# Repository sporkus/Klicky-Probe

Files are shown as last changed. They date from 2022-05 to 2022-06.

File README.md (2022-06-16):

# Klicky Probe
Microswitch probe with magnetic attachment, primarily aimed at CoreXY 3d printers.

Initially it was focused on the [Voron printers](https://vorondesign.com/) (V2.4, V1.8, Trident, V0) and derivatives, now it's been restructured to better allow other printers to be documented here.

The objectives for this project are:
- drop in replacement for Omron TL-Q5MC2 or PL-08N2 (you don't need to replace the toolhead), replacement of BLtouch probes
- soldering not required
- minimal adjustments required
- be able to detect all the print surfaces
- be as close to the hotend tip as possible
- highly repeatable and accurate probes
- less temperature variations
- no melting of its parts
- cheap to build
- reuse spare parts if possible

Most of the Klicky probe users are using klipper, there are some macros in here that ease the probing process, by automating the attach, dock and use of the probe.

Some work has been developed to have the same functionality on RRF.

It can also be used with the [automatic Z calibration](https://github.com/protoloft/klipper_z_calibration) klipper plugin to effectively calculate the Z offset from the probe and from the Z endstop if your printers supports a Z endstop triggered by the nozzle (like most Voron's do)

The inspiration for the Klicky Probe comes from the [Quickdraw](https://github.com/Annex-Engineering/Quickdraw_Probe) and the [Euclid probe](https://github.com/nionio6915/Euclid_Probe), it uses some concepts from each of the projects.

Updated instructions provided by StefanRaatz.
oc_geek and TurBoxxs were also a great help in refining and testing the CAD files.
Garrettwp provided the initial revised macro files.
User richardjm revised the macro variables and added some functions.
Mental created the initial macro and one of the first magnetically attached microswitch probes.

Without them, and some others this effort would not be in the current state, many thanks to them all.

It is working very well, if you decide to use it, give me feedback, either here, or on discord, my discord user is JosAr#0517.

If you want to donate something regarding this project, use this [link](https://paypal.me/Josar154) or [__Buy me some ABS!__](https://www.buymeacoffee.com/JosAr), thanks

# Upgrading from an earlier version

If you are upgrading from an earlier version, check the [klipper macros](./Klipper_macros) folder, it contains update instructions.

# Probe options

Right now, there are two probe attachment options, each with two probe types.

## Regular Klicky

First klicky probe, based on the [Quickdraw probe](https://github.com/Annex-Engineering/Quickdraw_Probe), with an added third magnet for added stability and fixed dock gantry setups.

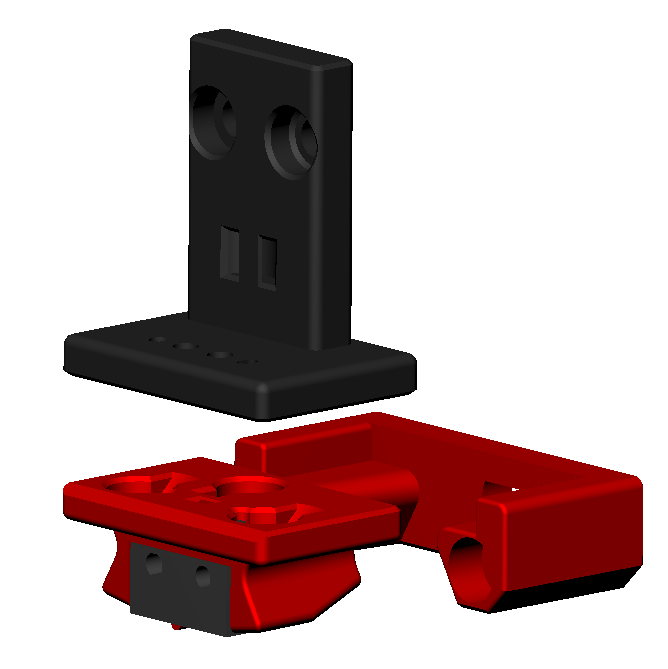
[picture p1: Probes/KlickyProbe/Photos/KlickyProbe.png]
klickyprobe


It uses magnets to secure the probe to the mount and also to make the electrical connection.
The magnets can be glued to prevent them from coming loose.
It supports a [microswitch probe](./Probes/KlickyProbe/) and [Unklicky](./Probes/UnklickyProbe/) ([invented by DustinSpeed](https://github.com/majarspeed/Unklicky)) (self built probe, that so far surpasses the microswitches in common use) based probing.

### [Assembly instruction](./Probes/KlickyProbe/)

## KlickyNG

New enclosed magnets probe, it does not require glue to help prevent the magnets from coming loose, magnets are also self aligning.
This approach only uses common and easy to source parts.

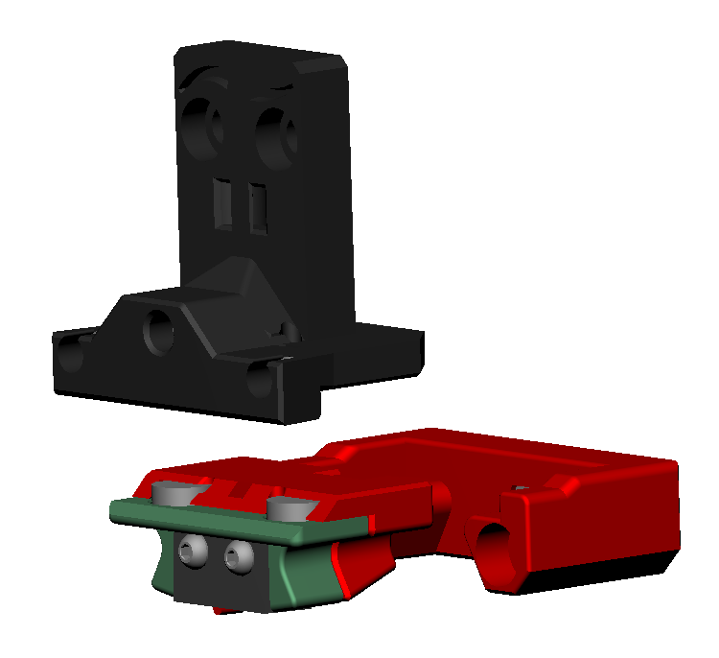
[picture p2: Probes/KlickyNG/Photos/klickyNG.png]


Also supports [microswitch probe](./Probes/KlickyNG/) and [Unklicky](./Probes/UnklickyNG/) ([invented by DustinSpeed](https://github.com/majarspeed/Unklicky)) (self built probe, that so far surpasses the microswitches in common use) based probing.

### [Assembly instruction](./Probes/KlickyNG/)

# Printers With detailed instructions and specific parts (by support order)

The specific parts with install, configuration, troubleshoot and recommended settings can be found on each printer page, linked below.

[Voron v2.4](./Printers/Voron/v1.8_v2.4_Legacy_Trident)

[Voron v1.8](./Printers/Voron/v1.8_v2.4_Legacy_Trident)

[Voron Legacy](./Printers/Voron/v1.8_v2.4_Legacy_Trident)

[Voron Trident](./Printers/Voron/v1.8_v2.4_Legacy_Trident)

[Voron v0](./Printers/Voron/v0)

[VCore-3](./Printers/Ratrig/VCore3)

[MercuryOne](./Printers/ZeroG/Mercury_One)

[Voron Switchwire](./Printers/Voron/Switchwire)

There are also [docks and mounts submitted by users](./Usermods) to support other printers and toolheads, you should check it out.

Klicky Probe imageklicky early version.

# Klicky components

All the compatible printers require:

* Toolhead mount (the thing that the probe attached to when it's being used)
* Klicky probe (there are three versions, all are interchangeable and compatible, more information on the specific printer page), what actually is used to probe the bed
* Probe dock (all the printers use the same)
* Probe dock mount (what attaches to the printer to dock the probe when not in use)

The CAD with all the files is located [Here](./CAD)

KlickyProbe STL's are now located on each probe type directory.

Printer specific STL are in each printer directory.

The klipper macros are [here](./Klipper_macros), the RRF [here](./RRF_macros).

## Probe accuracy

The probe accuracy output is better than a range of 0.025mm (difference between highest and lowest), and a standard deviation of 0.01mm.

## Print Settings

There are no need for supports, recommended settings are 4 perimeters/top/bottom, at least 23% infill, the STL's are already oriented, you only need to send them to the slicer.



Each printer family/version has it's own mounting options, Bill of Materials, assembly instructions and dock/attach setup.

# General Bill of Materials (BOM)

Tools:

- 1.5mm Drill (optional)
- Multimeter to check for Continuity 
- Super Glue
- Soldering Iron for the heat inserts

Probe BOM:

- 1x microswitch (the omron D2F-5 or D2F-5L (removing the lever) is recommended), D2F-1 and similar sizes microswitch also work
- 2x M2x10 mm self tapping
- some 6 mm x 3 mm magnets (it ranges from 8 to 10)
- some m5 screws
- some m3 screws
- some m3 heat inserts
- some m3 nuts

# Sourcing guide

To get the best experience, please consider purchasing from the trusted list of suppliers bellow.

[trusted suppliers list](./Sourcing.md)

# Assembled Klicky Probe on a Voron v2.4

# Assembled Klicky Probe

# Dock and undock video

https://user-images.githubusercontent.com/16675722/122302371-eb9c4e00-cef9-11eb-91d3-3aded131bae0.mp4

It is working very well, if you decide to use it, give me feedback, either here, or on Voron discord, my discord user is JosAr#0517.

By standing on the shoulders of giants, lets see if we can see further.

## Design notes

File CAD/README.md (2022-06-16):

CAD files

KlickyProbe_v2_v44
Initial release of the V2 klicky, with a 2mm shorter probe dock. Probe dock mounts adjusted accordingly

KlickyProbe_v2_v50
corrected dock mount fixed distance, it was 2 mm short

KlickyProbe_v2_v51
added MercuryOne probe dock

KlickyProbe_v2_v53
added VCore3 probe dock and EVA mount

KlickyProbe_v2_v54
added V0.1 Mosquito Cowling

KlickyProbe_v2_v55
corrected V0.1 integrated Mosquito Cowlings

KlickyProbe_v2_v56
updated the probe dock to have back inserted magnets, it's not possible now for the dock magnet to touch the probe one

KlickyProbe_v2_v57
Added V0.1 integrated Voron Revo Cowling

KlickyNGProbe_v4
Reduced the probe socket height, to better handle 2.7mm magnets

KlickyNGProbe_v5
Added a 3mm socket height, to better handle 3mm magnets

KlickyProbe_v2_v57
Added initial Switchwire servo dock

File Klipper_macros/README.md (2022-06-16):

# Klipper macros

These macros are  based on the great Annex magprobe dockable probe macros "#Originally developed by Mental, modified for better use on K-series printers by RyanG and Trails", kudos to them.
That macro as since evolved into a klipper plugin that currently is pending inclusion in klipper, more information [here](https://github.com/Annex-Engineering/Quickdraw_Probe/tree/main/Klipper_Macros)

Would alse like to thank the Voron discord community and VoronDesign for all the work, suggestions and support that they have given to improve on the macros.

## Updating from an earlier version

While you should read these instructions to the end, as the necessary helper functions are now split on different files and it's better explained below, as a current user of the klicky macros, it's easier to configure.

The first macro on the old klicky-probe.cfg contained all the necessary variables, you should the values you changed one by one to the new klicky-variables.cfg, the most important are these ones:

```ini
# if you do not have any of these variables, read the explanation on klicky-variables.cfg and the setup of the macros on your respective printer, this is a quick start quide
variable_enable_z_hop           # set this to false for beds that fall significantly under gravity (almost to Z max)
variable_max_bed_y              # bed max y size
variable_max_bed_x              # bed max x size

variable_z_endstop_x            # copy this value over your old file
variable_z_endstop_y            # copy this value over your old file

variable_docklocation_[x,y,z]   # copy this value over your old file
Variable_dockmove_[x,y,z]       # use 40,0,0 it's the old default
Variable_attachmove_[x,y,z]     # use 0,30,0 it's the old default
```

Now if you use auto-z calibration, you also should copy z-calibration.cfg to klicky-z-calibration.cfg and remove the z-calibration.cfg include in printer.cfg.

## New installation

The macros are currently separated by function, there is klicky-probe.cfg that should include the remaining files, this both keeps klipper's printer.cfg cleaner and allow for backward compatibility.

The remaining files are the klicky-macros.cfg that stores all the general macros (like the dock and attach macros, this file is required on all the printers), the klicky-variables.cfg where it's necessary to configure the dock location and do other printer specific configurations and the klipper helper files for specific functions.

The helper files work by expanding the standard klipper function with a attach and dock command, so that you can use all the klipper commands without the need to manually attach and dock the printer.

Right now the macros are divided in multiple files, that way it is much easier to upgrade, configure and maintain

| File | v2.4 | v1.8 | Legacy | Trident | Switchwire | v0 | Tiny-M | V-core3 | MercuryOne |
| --- | :---: | :---: | :---: | :---: | --- | :---: | :---: | :---: | --- |
| klicky-probe.cfg | :heavy_check_mark: | :heavy_check_mark: | :heavy_check_mark: | :heavy_check_mark: | :heavy_check_mark: | :heavy_check_mark: | :heavy_check_mark: | :heavy_check_mark: | :heavy_check_mark: |
| klick-variables.cfg | :heavy_check_mark: | :heavy_check_mark: | :heavy_check_mark: | :heavy_check_mark: | :heavy_check_mark: | :heavy_check_mark: | :heavy_check_mark: | :heavy_check_mark: | :heavy_check_mark: |
| klicky-bed-mesh-calibrate.cfg | :heavy_check_mark: | :heavy_check_mark: | :heavy_check_mark: | :heavy_check_mark: | :heavy_check_mark: | :heavy_check_mark: | :heavy_check_mark: | :heavy_check_mark: | :heavy_check_mark: |
| Klicky-quad-gantry-level.cfg | :heavy_check_mark: | :x: | :x: | :x: | :x: | :x: | :x: | :x: | :x: |
| Klicky-screws-tilt-calculate.cfg | :x: | :heavy_check_mark: | :heavy_check_mark: | :x: | :x: | :heavy_check_mark: | :heavy_check_mark: | :x: | :grey_question: |
| klicky-z-tilt-adjust.cfg | :x: | :heavy_check_mark: | :heavy_check_mark: | :heavy_check_mark: | :heavy_check_mark: | :x: | :x: | :heavy_check_mark: | :heavy_check_mark: |

* klicky-probe.cfg (includes all the necessary files in klipper)
* klick-variables.cfg, stores all the Klicky variables, printer specific, should not be necessary to update very often
* klicky-bed-mesh-calibrate.cfg, bed mesh helper scripts, assumes bed mesh is already configured, includes a commented example, further help on setup [here](https://www.klipper3d.org/Bed_Mesh.html#bed-mesh)
* Klicky-quad-gantry-level.cfg, Quad Gantry Level helper script, allows on machines with four Z independent motors to level the bed automatically, assumes QGL is already configured (it's used on a V2.4 to level the gantry relative to the bed), further help [here](https://www.klipper3d.org/Config_Reference.html?h=quad#quad_gantry_level)
* Klicky-screws-tilt-calculate.cfg, screws tilt adjust helper script, knowing where the bed screws are, it will assist in leveling the bed by calculating on the number of times each screw should be rotated, assumes that the configuration is already defined, further help on setup [here](https://www.klipper3d.org/Manual_Level.html#adjusting-bed-leveling-screws-using-the-bed-probe)
* klicky-z-tilt-adjust.cfg, Z tilt adjust helper script, allows on machines with two or three Z independent motors to level the bed automatically, assumes that the configuration is already defined, further help on setup [here](https://www.klipper3d.org/Config_Reference.html?h=z_tilt#z_tilt)
* klicky-specific.cfg, place to put other configurations specific to your printer, like probe or bed mesh klipper configuration

Some printers, like the Voron v0 or Tiny-M don't have the probe as a standard configuration, so in those printers documentation there are extra klipper configurations that you need to use in order to configure the actual probe.

## printer.cfg configuration 

Download the appropriate files (or the zip containing them all and delete the ones that are not relevant) and upload it to your klipper Config folder.

```bash
cd ~/klipper_config/
wget https://raw.githubusercontent.com/jlas1/Klicky-Probe/main/Klipper_macros/Klipper_macros.zip
unzip Klipper_macros.zip
```

Check the klicky-probe.cfg, remove or comment the macros that are not required for your printer or that you do not want to implement.
Edit klicky-variables.cfg (there are printers specific recommendations on the printer configuration page) for klicky to operate properly.

There are some configurations that need to be checked, otherwise your will run into **out of range** problems, that is by design.

Open your printer.cfg file, comment out *safe_z_home* or *homing_override*, if you have them (the macros will take care of homing) and add the following line before the "Macros" Section.

`[include klicky-probe.cfg]`

It should look like this:

```ini
#####################################################################
# 	Macros
#####################################################################
[include klicky-probe.cfg]
```

You now need to configure the probe pin, that is printer specific, and the details are on your printer configuration guide.

Regarding you print start and end macros, with the helper scripts implemented, they do not need to be changed.

If however you would like to reduce the times that the toolhead attaches and docks the probe, you can use Attach_Probe_Lock that prevents the probe to be docked after an operation that normally would dock the probe.

**BEWARE that the probe may hit the bed depending on what you are doing**.

When you don't need the probe attached anymore, run Dock_Probe_Unlock to dock and unlock the probe.

## Pre and Post macros for dock operations

If your setup requires a custom move, a macro to be called before attaching and docking, there are two macros **\_DeployDock** and **\_RetractDock** that are executed (if they are configured) when it's required for the dock to be ready for docking and attachment operations.

Currently, thanks to Kyleisah there is also support to use a simple servo setup, when a certain angle deploys the dock and another retracts it, you can find the following variables on klicky-variables.cfg.

```ini
#The following variables are used if the dock is deployed and retracted via a servo motor
variable_enable_dock_servo:  False    # Set to true if your klicky dock is servo-controlled
variable_servo_name:        'NAME'    # The name of the dock servo defined in printer.cfg under [servo]
variable_servo_deploy:          10    # This EXAMPLE is the value used to deploy the servo fully
variable_servo_retract:         11    # This EXAMPLE is the value used to retract the servo fully (initial_angle in [servo] config)
variable_servo_delay:         1000    # This is a delay to wait the servo to reach the requested position, be carefull with high values
```

On printer.cfg to add servo support, you need to add the following:

```ini
[servo klicky_servo]
pin: PC12
#   PWM output pin controlling the servo. This parameter must be
#   provided.
maximum_servo_angle: 180
#   The maximum angle (in degrees) that this servo can be set to. The
#   default is 180 degrees.
minimum_pulse_width: 0.00025
#   The minimum pulse width time (in seconds). This should correspond
#   with an angle of 0 degrees. The default is 0.001 seconds.
maximum_pulse_width: 0.0024
#   The maximum pulse width time (in seconds). This should correspond
#   with an angle of maximum_servo_angle. The default is 0.002
#   seconds.
```

To increase the servo strength, you should connect the servo 5v to a PSU instead of to the MCU.

## Status leds

Thanks to foonietunes we now have status leds support (specially useful for SB leds).

[You can read how to implement it here](https://github.com/VoronDesign/Voron-Afterburner/tree/sb-beta/Klipper_Macros).

## XY Sensorless homing 

If you are using sensorless homing, and have your own X and/or Y homing macros, you can use override the klicky macros behavior with your very own _HOME_X and _HOME_Y macros.

If they exist on your klipper configuration, klicky macro will use them instead of the default G28 commands.

## Euclid support

To support euclid side dock and undock, try these values

```python
#Attach move. final toolhead movement to attach the probe on the mount
#it's a relative move
Variable_attachmove_x:          -70
Variable_attachmove_y:            0
Variable_attachmove_z:         1000

#Attach move2
Variable_attachmove2_x:          0
Variable_attachmove2_y:         40
Variable_attachmove2_z:       1000

#Dock move, final toolhead movement to release the probe on the dock
#it's a relative move
Variable_dockmove_x:              0
Variable_dockmove_y:            -40
Variable_dockmove_z:           1000
```

**you need to check whay is the Z height of the Euclid Dock to replace the 1000 z moves above**

## Advanced users

**Beware going forward, you will leave the safety that the macros provide**

I recognize that some users are very technical and may want to write custom macros, so here are the only commands that you need to  attach and dock the probe, without any fail safes or checks.

### Probe attach commands

```python
# Probe entry location
G0 X{docklocation_x|int - attachmove_x|int - attachmove2_x|int} Y{docklocation_y|int - attachmove_y|int - attachmove2_y} F{travel_feedrate}
# Attach probe
G0 X{docklocation_x|int - attachmove2_x|int} Y{docklocation_y|int - attachmove2_y} F{travel_feedrate}
G0 X{docklocation_x} Y{docklocation_y} F{dock_feedrate}
# Probe exit location
G0 X{docklocation_x|int - attachmove_x|int} Y{docklocation_y|int - attachmove_y|int} F{release_feedrate}
```

### Probe dock commands

```python
# Probe entry location
G0 X{docklocation_x|int - attachmove_x|int} Y{docklocation_y|int - attachmove_y|int} F{travel_feedrate}
# Drop Probe to Probe location
G0 X{docklocation_x} Y{docklocation_y} F{dock_feedrate}
# Probe decoupling
G0 X{docklocation_x|int + dockmove_x|int} Y{docklocation_y|int + dockmove_y|int} F{release_feedrate}
G0 X{docklocation_x|int + dockmove_x|int - attachmove_x|int} Y{docklocation_y|int + dockmove_y|int - attachmove_y|int} F{release_feedrate}
```

The typical variables values are:

```ini
variable_travel_speed:          100    # how fast all other travel moves will be performed when running these macros
variable_dock_speed:             50    # how fast should the toolhead move when docking the probe for the final movement
variable_release_speed:          75    # how fast should the toolhead move to release the hold of the magnets after docking
#Dock move (if the dock is mounted on the back extrusion, these values can be left untouched)
Variable_dockmove_x:              0    # Final toolhead movement to release
Variable_dockmove_y:             40    # the probe on the dock
Variable_dockmove_z:              0    # (can be negative)
#Attach move (if the dock is mounted on the back extrusion, these values can be left untouched)
Variable_attachmove_x:           30    # Final toolhead movement to Dock
Variable_attachmove_y:            0    # the probe on the dock
Variable_attachmove_z:            0    # (can be negative)

Variable_attachmove2_x:           0    # intermediate toolhead movement to attach
Variable_attachmove2_y:           0    # the probe on the dock (can be negative)
Variable_attachmove2_z:           0    # (to be used as a last move before attaching the probe, suitable for Euclid)
```

**Again, be advised that these will not raize the bed to avoid hitting it, won't check if the probe is docked or attached. USE EXTREME CAUTION**

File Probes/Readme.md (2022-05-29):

# Probe options

Right now, there are two probe attachment options, each with two probe types.

## Regular Klicky

First klicky probe, based on the [Quickdraw probe](https://github.com/Annex-Engineering/Quickdraw_Probe), with an added third magnet for added stability and fixed dock gantry setups.

klickyprobe

It uses magnets to secure the probe to the mount and also to make the electrical connection.
The magnets can be glued to prevent them from coming loose.
It supports a [microswitch probe](./KlickyProbe/) and [Unklicky](./UnklickyProbe/) ([invented by DustinSpeed](https://github.com/majarspeed/Unklicky)) (self built probe, that so far surpasses the microswitches in common use) based probing.

#### [Assembly instruction](./KlickyProbe/)

## KlickyNG

New enclosed magnets probe, it does not require glue to help prevent the magnets from coming loose, magnets are also self aligning.
This approach only uses common and easy to source parts.

klickyNGprobe

Also supports [microswitch probe](./KlickyNG/) and [Unklicky](./UnklickyNG/) ([invented by DustinSpeed](https://github.com/majarspeed/Unklicky)) (self built probe, that so far surpasses the microswitches in common use) based probing.

#### [Assembly instruction](./KlickyNG/)

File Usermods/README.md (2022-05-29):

# Klicky usermods

Here you can find Klicky user submitted mods to support extra printers and toolheads, mods that support a printer with specific documentation (Like the Vorons ot the Vcore3) have a dedicated usermod directory in the specific printer directory.

All the compatible printers require:

* Toolhead mount (the thing that the probe attached to when it's being used), it's toolhead specific
* Klicky probe (there are three versions, all are interchangeable and compatible, more information on the specific printer page), what actually is used to probe the bed, the parts are equal on all the printers
* Probe dock (all the printers use the same), the parts are equal on all the printers
* Probe dock mount (what attaches to the printer to dock the probe when not in use), should be printer specific and not toolhead specific

The recommended macros can be found [here for klipper](..//Klipper_macros) macros and [here for RRF](../RRF_macros).

There are two types of user mod:

* Printer dock mount (identified by "dock mount")
* Toolhead probe mount (identified by "probe mount")

| Owner | Descrption | Mod Type | Printer/Toolhead |
| --- | --- | --- | --- |
| TheMacBoy | [support arm for Ender 5 Plus with rails](./TheMacBoy) | dock mount  | Ender 5 Plus |
| TheMacBoy | [Klicky Probe mount for EVA](./TheMacBoy) | probe mount | EVA 2.2+ |
| DoubleT | [Klicky Probe mount for EVA Trihorn UHF fan duct](./DoubleT) | probe mount | EVA 2.4+ |
| SSerpente | [Klicky Probe mount for VzBot](./SSerpente) | dock mount  | VzBot |

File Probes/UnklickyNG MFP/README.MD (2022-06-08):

## UnklickyNG BFP (WIP)

#### Printing

* Forced 0.4mm perimeter
* 5 bottom and top layer 
* 30% + infill 

#### BOM 

* 5 - 6x3mm magnets
* 1 - M3x16mm SHCS 
* 1 - M3x6mm SHCS or BHCS
* 1 - M2x12mm or M2x10mm self tapping screw 
* 60mm 24awg wires 

#### Assembly

1. Insert fixed wire. Screw in m3x16 just enough to fix the wire

2. Fix pin wire in pin with m3x6. Add magnet and insert into the body.

3. Screw m3x16 the whole way in

4. Add backpocket magnet

5. Put the back magnet in cap and put the cap on partially

6. Slide two front magnets in and tighten the cap completely

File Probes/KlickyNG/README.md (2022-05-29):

# Klicky Probe NG (Next Generation)
Microswitch probe with magnetic attachment, primarily aimed at CoreXY 3d printers, with enclosed magnets, don't fall, don't need to be glued.

This version is still a **BETA** version, so please use with care.
Its parent version, and still the recommended one is [Klicky](../KlickyProbe/).

The objectives for this project are:
- drop in replacement for Omron TL-Q5MC2 or PL-08N2 (you don't need to replace the toolhead), replacement of BLtouch probes
- no soldering required
- minimal adjustments required
- be able to detect all the print surfaces
- be as close to the hotend tip as possible
- highly repeatable and accurate probes
- less temperature variations
- no melting of its parts
- reuse spare parts if possible
- no need to use hard to source parts
- no need to glue the magnets

For now this document will only deal with KlickyNG-specific wiring; for all the rest of the configuration, please follow the [main guide](https://github.com/jlas1/Klicky-Probe).

The inspiration for the Klicky Probe comes from the [Quickdraw](https://github.com/Annex-Engineering/Quickdraw_Probe) and the [Euclid probe](https://github.com/nionio6915/Euclid_Probe), it uses some concepts from each of the projects, but with this version, it expands on the concept, as the method that it uses was developed independently. 

Please check the main Klicky repository for all the people that helped this project, for NG, would like to thank (in no specific order) Dustinspeed, Drachenkatze, clee, maz and whoppingpochard.

If you want to donate something regarding this project, use this [link](https://paypal.me/Josar154) or [__Buy me some ABS!__](https://www.buymeacoffee.com/JosAr), thanks

Without further delay, here is the new version with enclosed magnets:
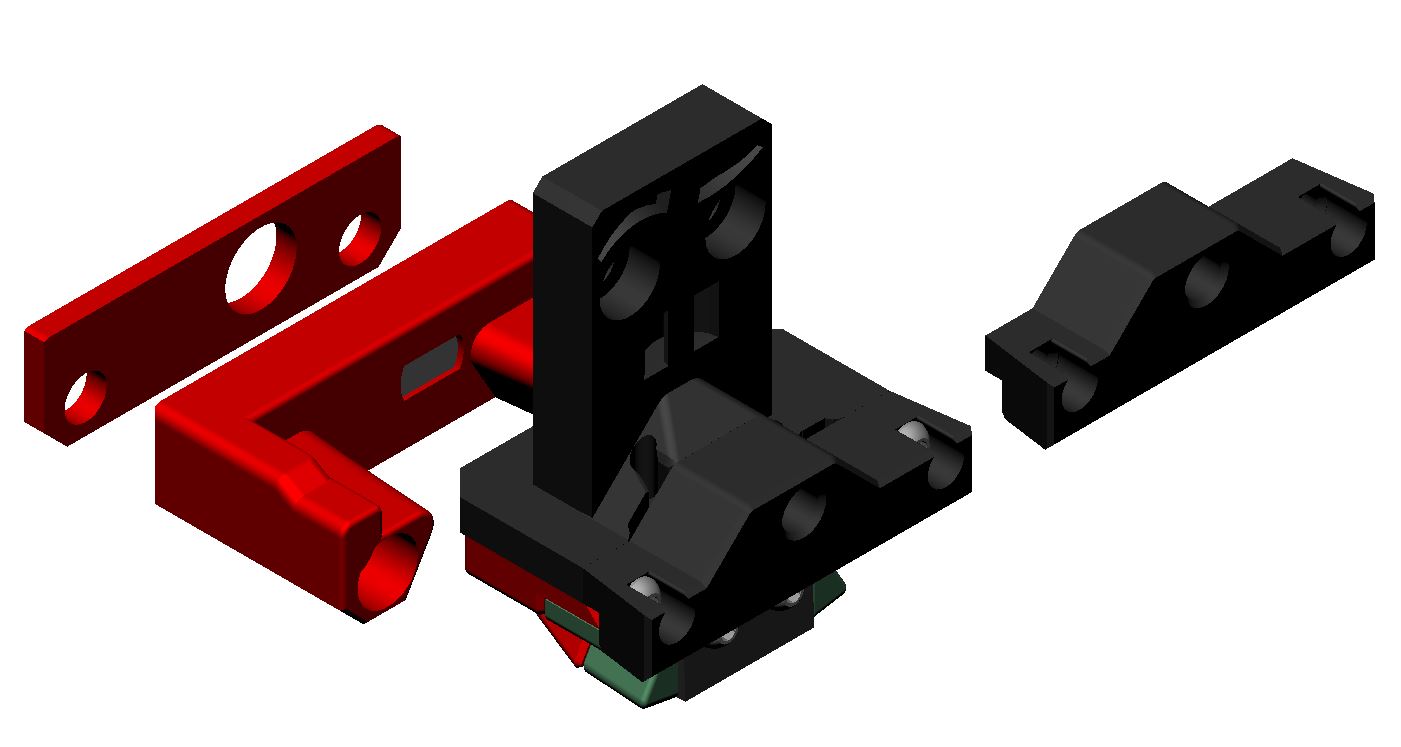
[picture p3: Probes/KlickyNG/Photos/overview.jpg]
Klicky Probe image


The eyebrows are clee+whoppingpochard's design.

# KlickyNG support

For now, only printers compatible with Voron StealthBurner/AfterBurner are compatible, as the NG mount has changed significantly and needs to be ported to the other mounts.

- [The CAD with all the files](../../CAD)
- [STL Files](./STL)

The arms are compatible with both Klicky and KlickyNG.

There is also [an exploded view](https://youtu.be/mlyU2tHjebo).

## Print Settings

There is no need for supports; recommended settings are 4 perimeters/top/bottom, at least 23% infill. The STL's are already oriented for you, so you only need to send them to the slicer.

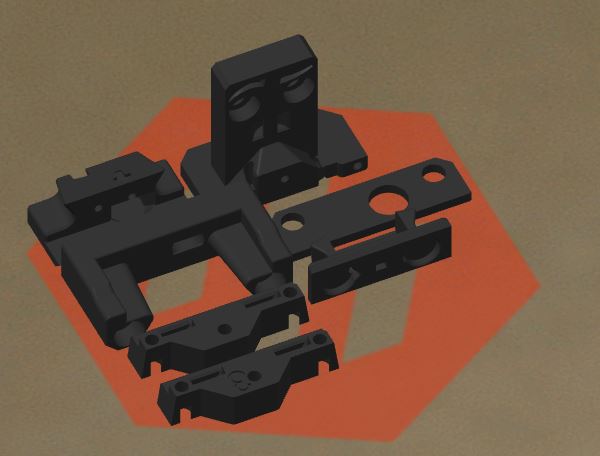
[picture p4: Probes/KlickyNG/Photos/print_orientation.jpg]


## Required parts

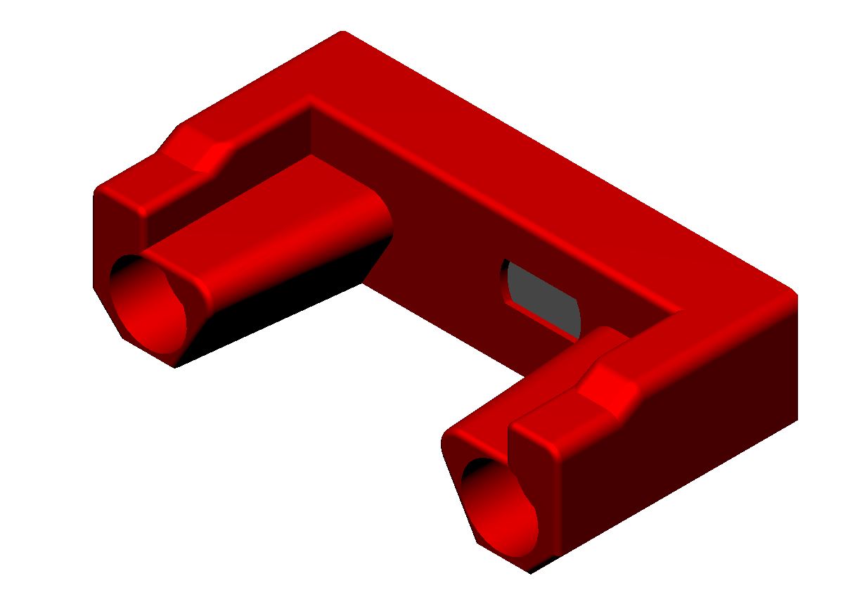
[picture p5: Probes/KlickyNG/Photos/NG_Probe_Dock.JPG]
NG_Probe_Dock
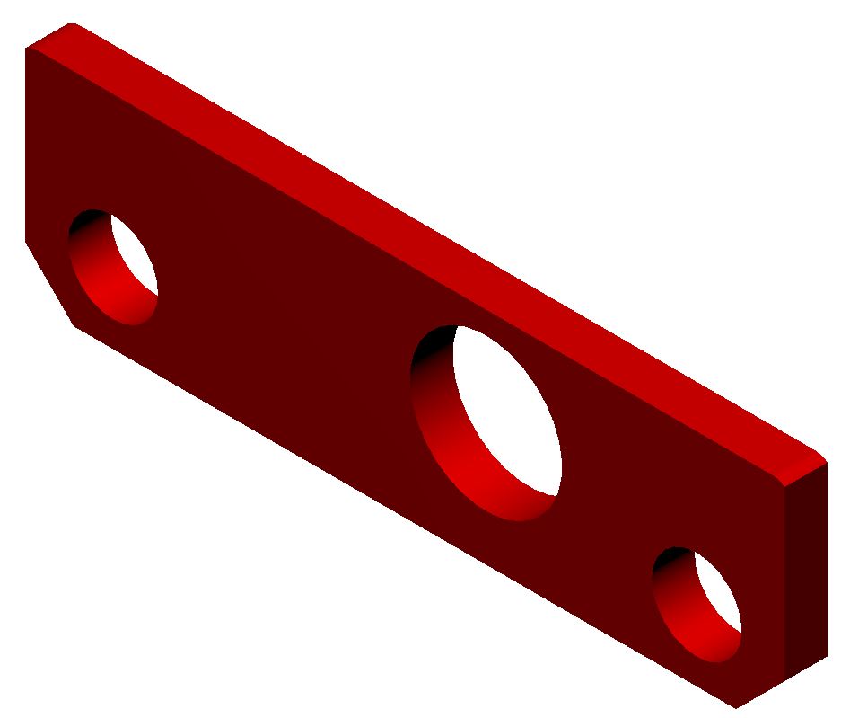
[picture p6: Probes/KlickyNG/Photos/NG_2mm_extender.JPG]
NG_2mm_extender
|  | If you want to reuse your old Klicky dock, it needs to use this setup for the back magnet. It will also be necessary to print the 2mm NG extender, as the dock needs to be 2mm longer. |
| :---: | --- |
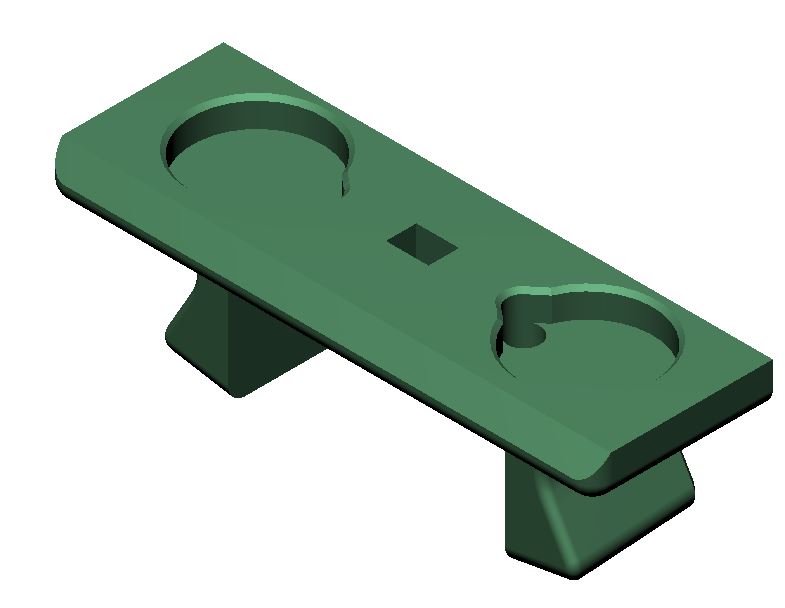
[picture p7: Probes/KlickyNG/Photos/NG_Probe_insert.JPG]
NG_Probe_insert
|  | Probe Insert, required to hold the switch and the two magnets that make the electrical connection |
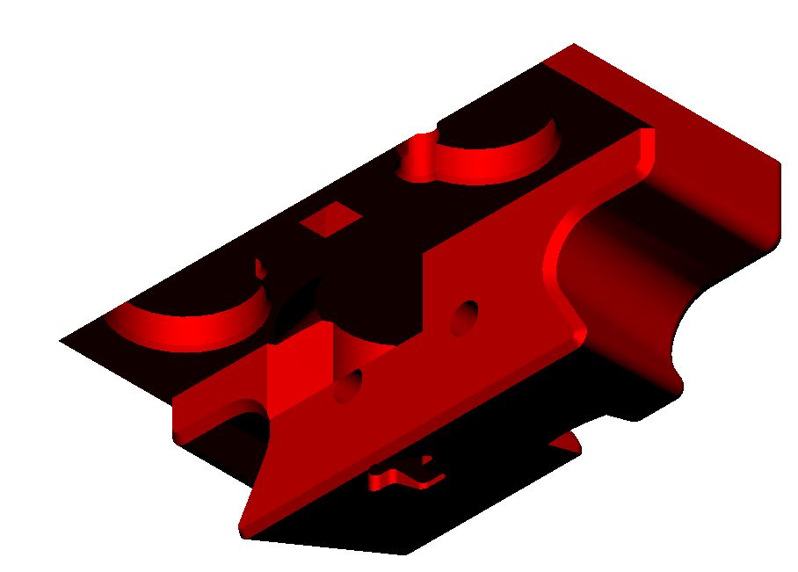
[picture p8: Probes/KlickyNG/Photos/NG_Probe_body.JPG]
NG_Probe_body
|  | Probe body, required to prevent the two front magnets from escaping the probe, holds the third magnet to help attach the probe to the mount and the back magnet to secure it to the dock |
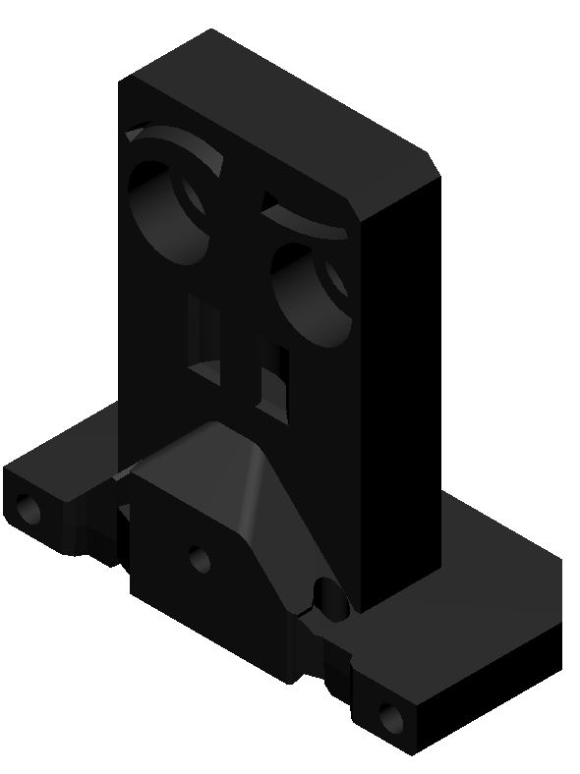
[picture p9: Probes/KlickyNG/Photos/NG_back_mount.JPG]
NG_back_mount
|  | Mount back, mounts to the AB/SB, holds the third magnet and the wire connections |
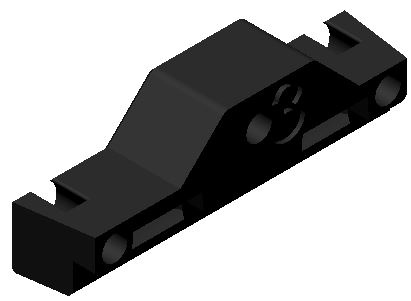
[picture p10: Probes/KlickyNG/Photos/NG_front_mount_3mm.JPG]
NG_front_mount_3mm
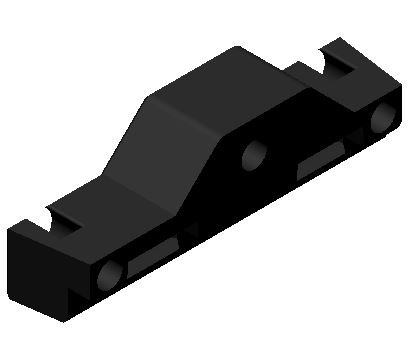
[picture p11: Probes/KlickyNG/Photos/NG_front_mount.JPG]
NG_front_mount
|  | Mount front, 2 versions; one for around 2.75mm (instead of 3mm) height, and one for actual 3mm-height magnets |

# Bill of Materials (BOM)

- 1x microswitch (the Omron D2F-5, or D2F-5L with the lever removed, are recommended, but similar-sized microswitches like D2F-1 and KW10 will also work)
- 30cm of wire, AWG22 or similar
- 5 M2x10mm self-tapping screws
- 8x 6mm diameter x 3mm height magnets
- 2x M3x18mm/M3x20mm screws

# Build Process

First, assemble the required materials.

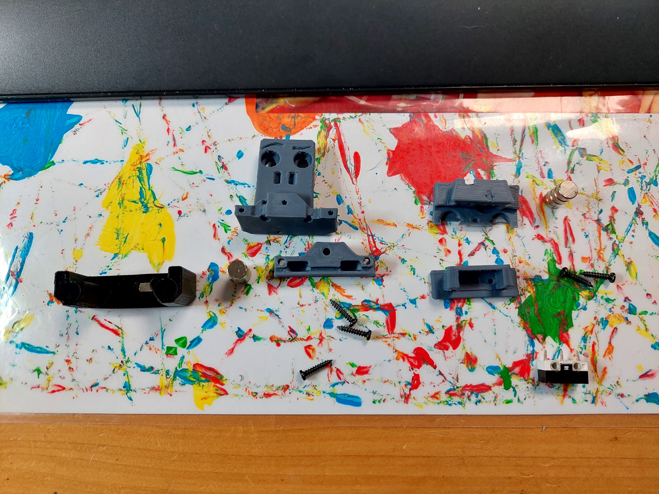
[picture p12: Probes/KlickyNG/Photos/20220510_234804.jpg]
material


## Probe assembly

- Put two magnets on the KlickyNGProbe_v3 Insert, and make sure they have the same polarity.
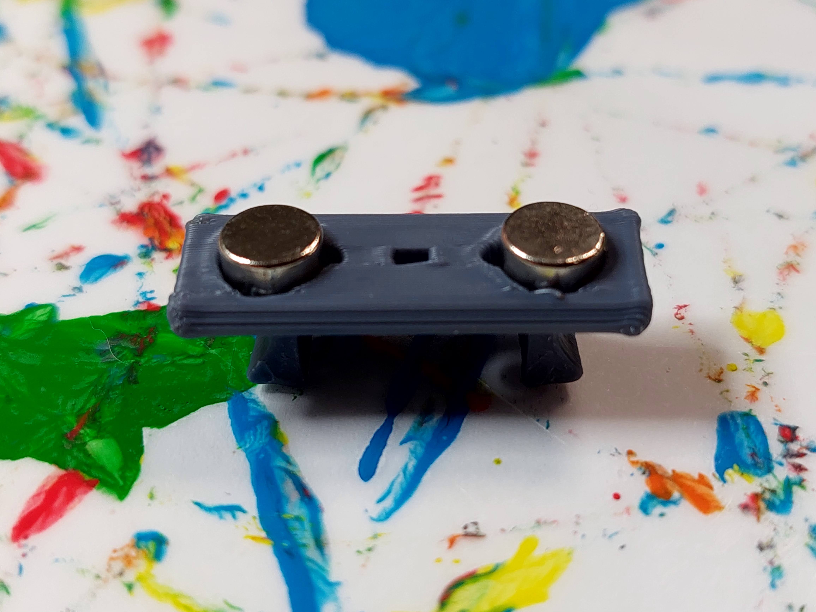
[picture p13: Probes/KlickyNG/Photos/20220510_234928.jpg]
  
- Next, insert another magnet on the back groove of the KlickyNGProbe_v3 Body. In this image, all 3 magnets should have the same polarity on top, so that when they are assembled, the back magnet will repulse the two front magnets.
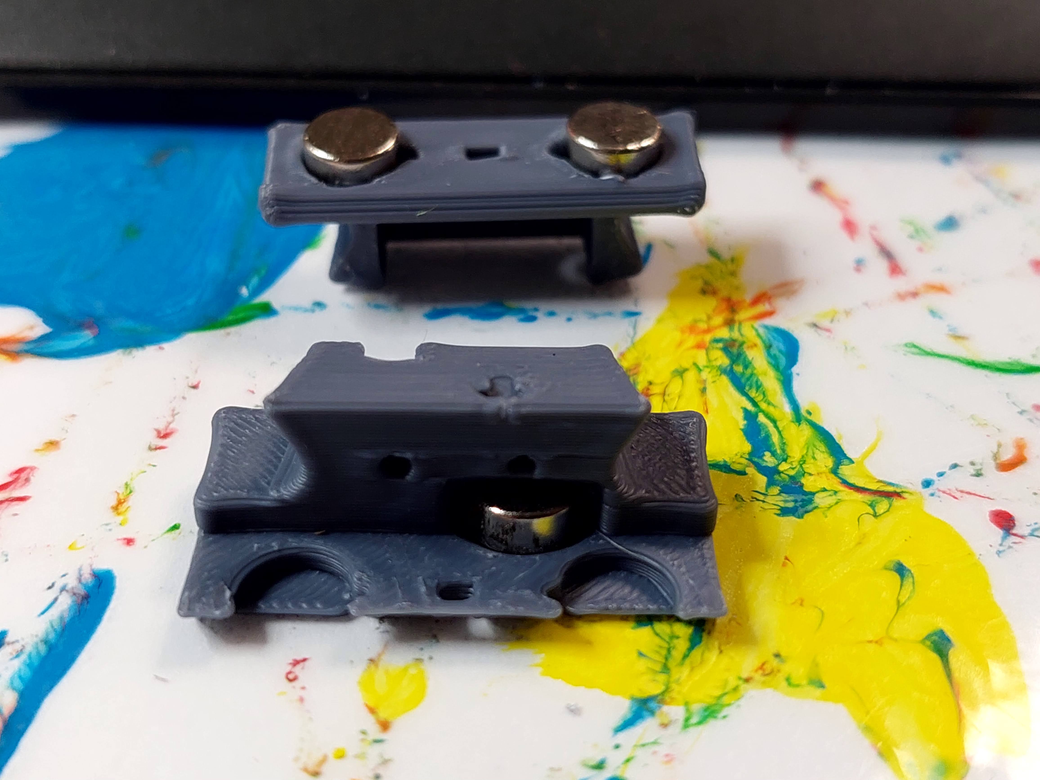
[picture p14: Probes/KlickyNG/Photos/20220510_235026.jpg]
  
- Now, place the insert on the body, aligning the magnets and making sure that the front magnets do not move out of place.
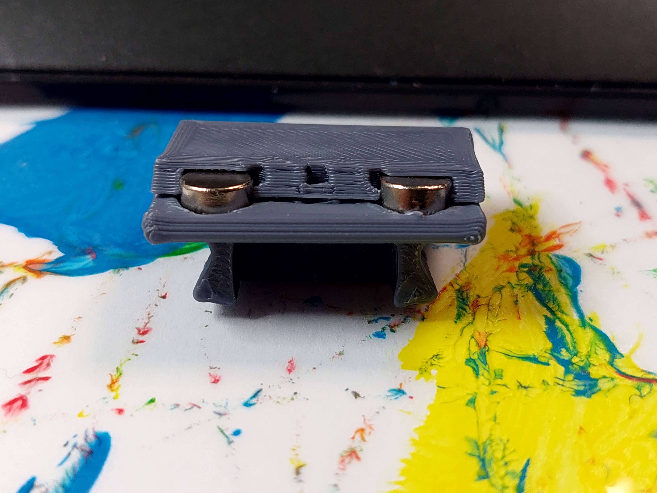
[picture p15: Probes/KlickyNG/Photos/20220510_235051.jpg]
  
- Insert the microswitch in its place (pictured here a KW10)
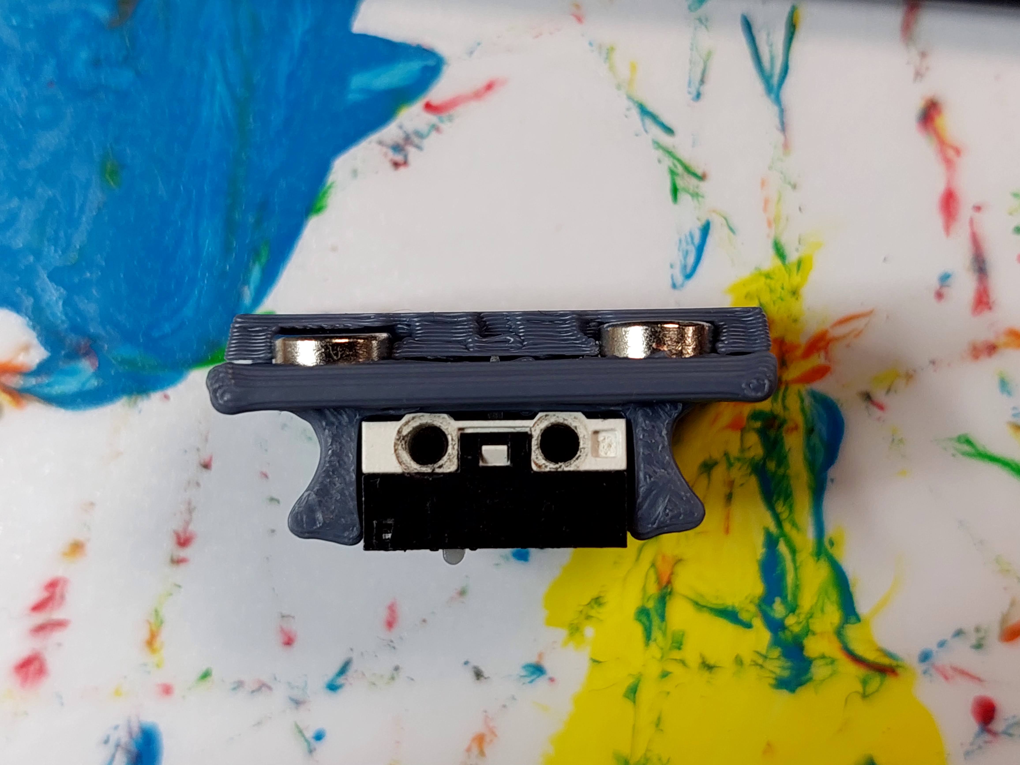
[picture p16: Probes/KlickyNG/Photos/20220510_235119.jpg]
  
- Secure the microswitch with the two M2x10 screws to secure the switch, and also pull the two parts of the probe body together.
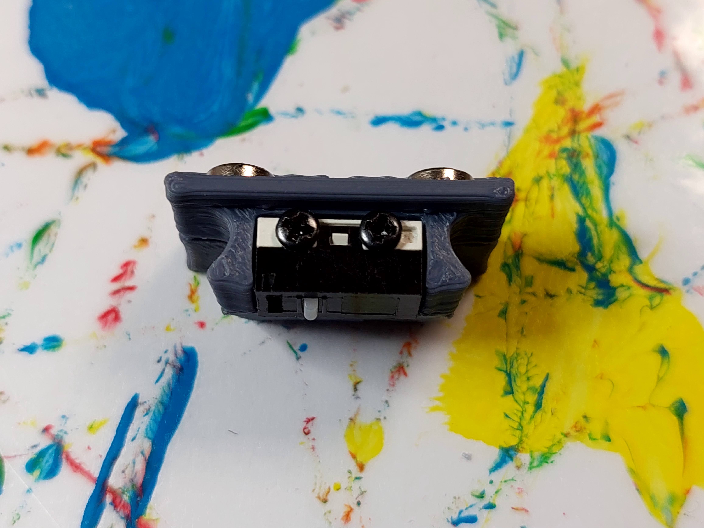
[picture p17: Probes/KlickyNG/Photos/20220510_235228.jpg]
  
- Insert the back magnet, and the probe is complete!
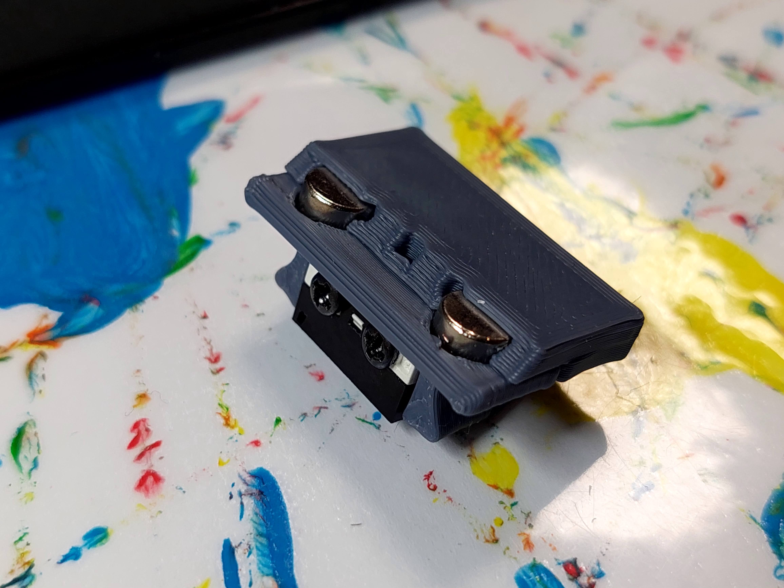
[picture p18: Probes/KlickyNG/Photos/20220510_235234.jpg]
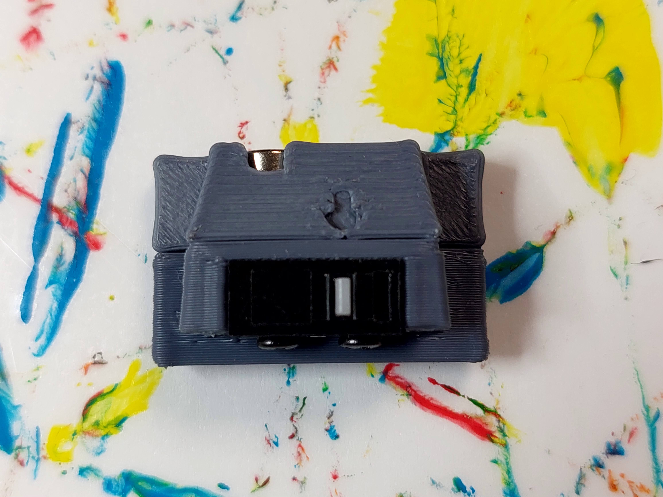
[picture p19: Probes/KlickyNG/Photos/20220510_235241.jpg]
  |  |  |
  | ------------------------------------------------------------ | ------------------------------------------------------------ |

## AB/SB mount assembly

- Cut the 30cm of wire in half to create two 15cm lengths of wire. Remove 7-8mm of insulation, and rotate the core to prevent loose wires.
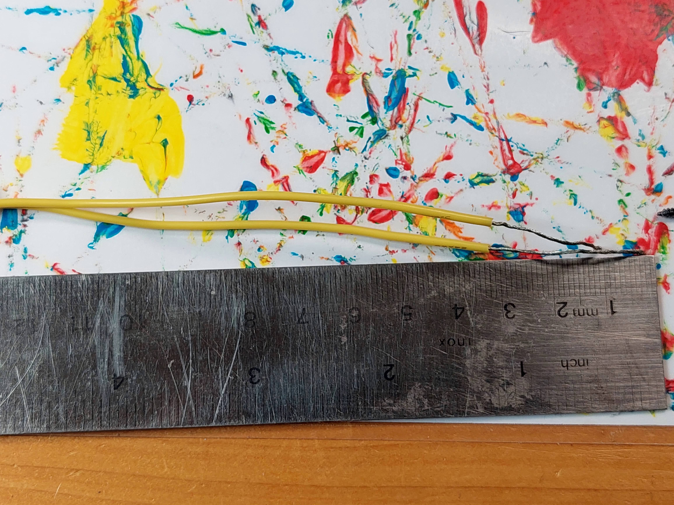
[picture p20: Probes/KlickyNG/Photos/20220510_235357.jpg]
  
- Insert the wire on the holes on the back mount
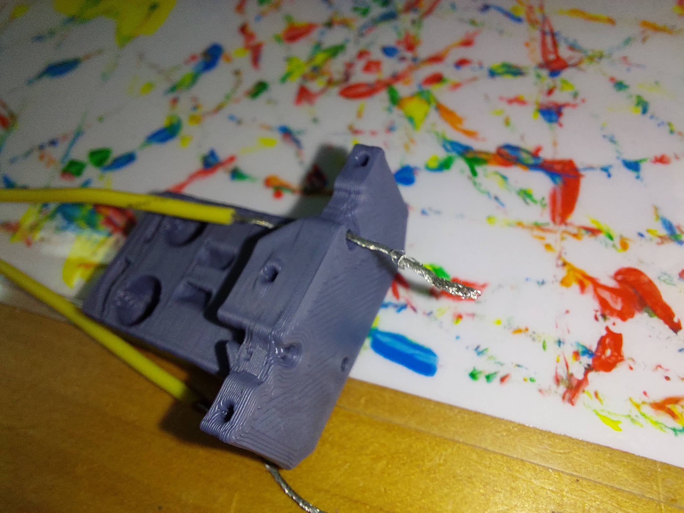
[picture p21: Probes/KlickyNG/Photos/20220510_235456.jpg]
  
- Rotate the wires around the other end to prevent them from escaping when the mount is being assembled
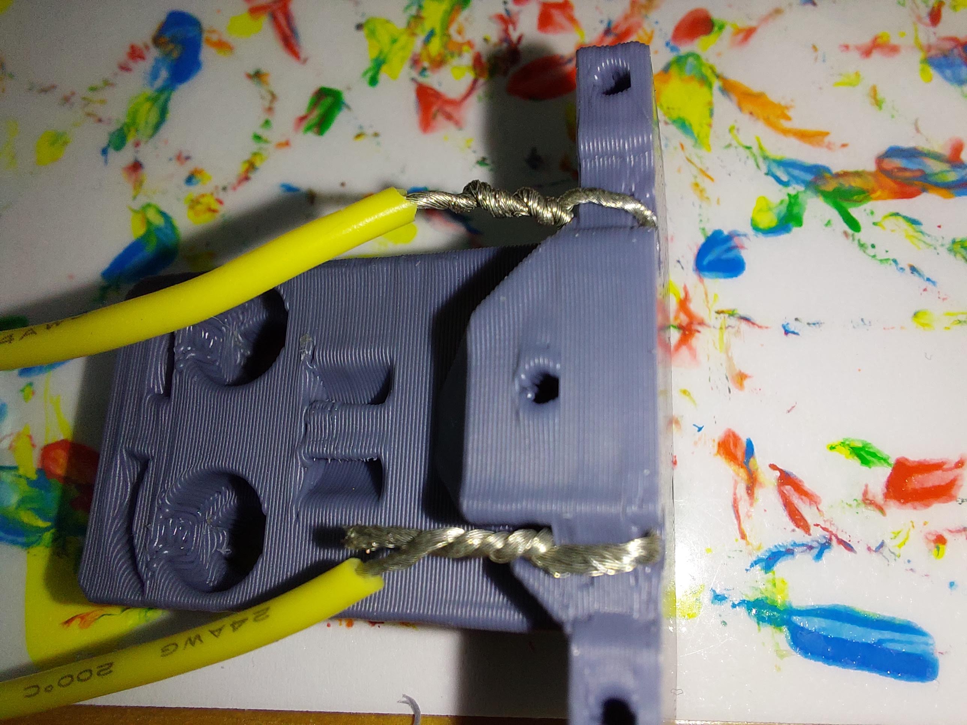
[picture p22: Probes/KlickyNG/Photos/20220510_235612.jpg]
  
- Put two magnets on top on the probe front magnets
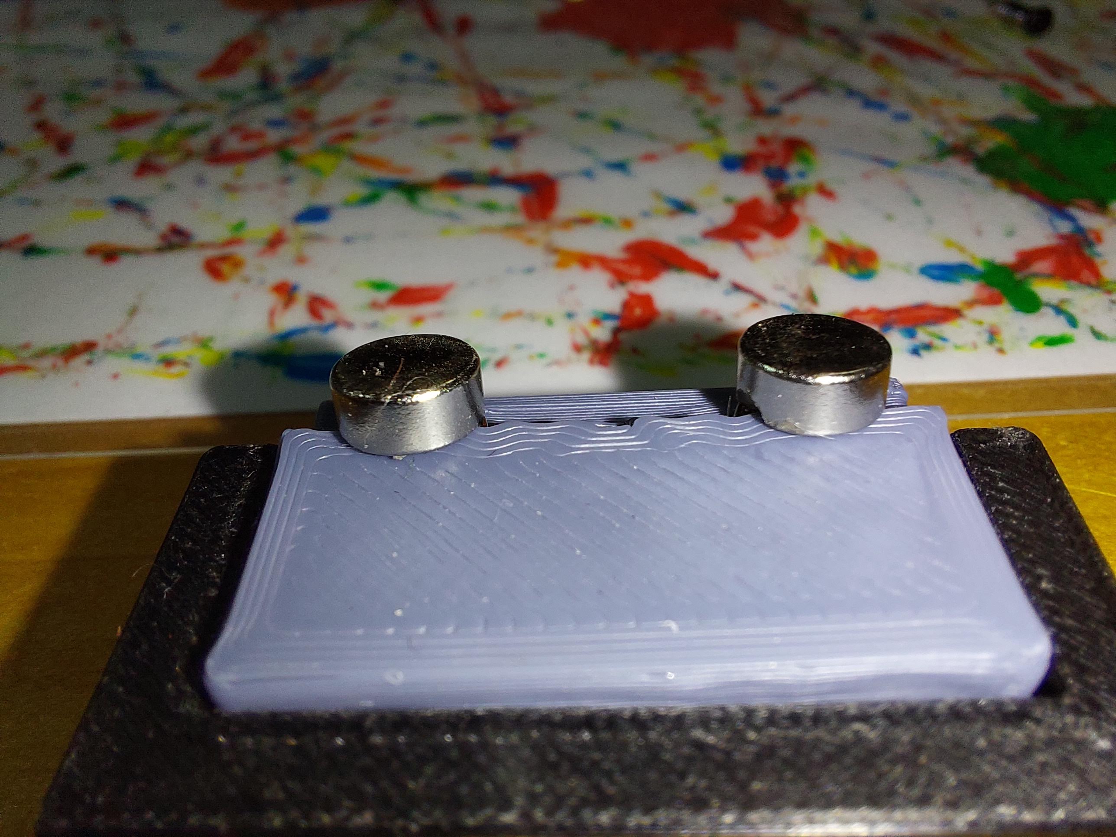
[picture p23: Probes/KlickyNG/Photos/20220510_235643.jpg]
  
- Insert the correct front mount on the magnets so that they remain attracted to the probe.
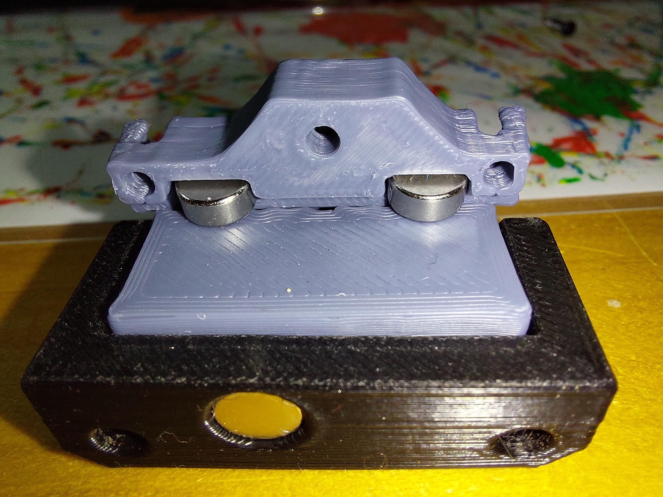
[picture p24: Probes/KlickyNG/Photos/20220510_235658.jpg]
  
- with the magnets and front secure, joint the mount front and back with an m2 screw
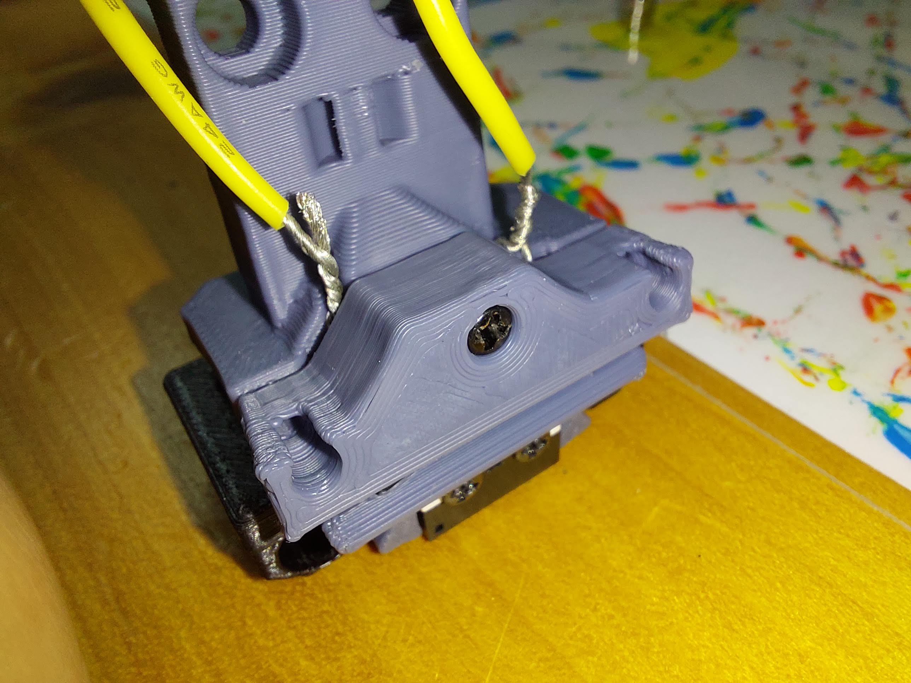
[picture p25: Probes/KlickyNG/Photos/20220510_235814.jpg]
  
- Now, complete with the remaining two m2 screws that will keep the front level
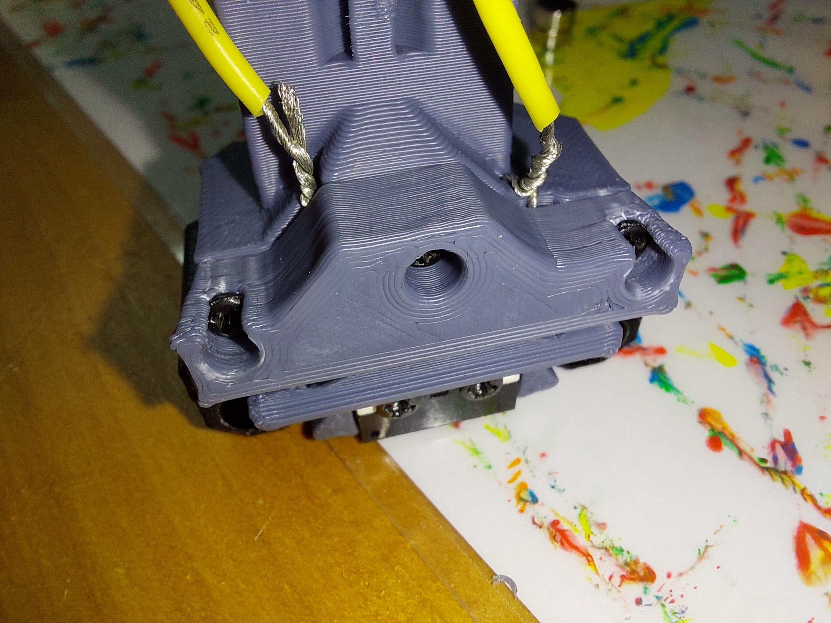
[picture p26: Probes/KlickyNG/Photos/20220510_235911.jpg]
  
- Attach another magnet on the 3rd probe magnet
  
- Respecting its polarity, put it into the mount back magnet socket
  
- The mount is now assembled!
  |  |  |
  | ------------------------------------------------------------ | ------------------------------------------------------------ |

## Final thoughts

For the installation, you should now replace the dock (or add the extender to your existing dock) and mount the probe mount to AB or SB and test it. You shouldn't need to change any configuration on your printer, if Klicky was already running without problems.

I have tested Aliexpress N35, N42 and N45 (graciously provided by Drachenkatze) with over 2000 attach/probe/dock without a single probe or dock operation failure.

Please test and report, but remember, **this is a BETA! It may twist your extrusions, or ruin your print surface. Use with care.**

There will also be soon a [Unklicky](https://github.com/majarspeed/Unklicky) for KlickyNG, stay tuned.

It is working very well for me. If you decide to use it, please send me feedback, either here, or on Voron discord. My discord username is `@JosAr#0517`.

By standing on the shoulders of giants, let's see if we can see further.

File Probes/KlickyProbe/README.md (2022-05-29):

# Klicky Probe
Microswitch probe with magnetic attachment, primarily aimed at CoreXY 3d printers.

KlickyProbe

The objectives for this project are:

- drop in replacement for Omron TL-Q5MC2 or PL-08N2 (you don't need to replace the toolhead), replacement of BLtouch probes
- no soldering required
- minimal adjustments required
- be able to detect all the print surfaces
- be as close to the hotend tip as possible
- highly repeatable and accurate probes
- less temperature variations
- no melting of its parts
- reuse spare parts if possible
- no need to use hard to source parts

## Print Settings

There is no need for supports; recommended settings are 4 perimeters/top/bottom, at least 23% infill. The STL's are already oriented for you, so you only need to send them to the slicer.

print_orientation

## Required parts

| NG_Probe_Dock | Klicky dock, it secures the probe to the dock via an extra magnet.<br />Allows to pull the probe by at least 2mm away |
| :---: | --- |
| Probebody | Probe body |

The required files are located here:

- [CAD files](../../CAD)
- [STL files](./STL)

# Bill of Materials (BOM)

- 1x microswitch (the Omron D2F-5, or D2F-5L with the lever removed, are recommended, but similar-sized microswitches like D2F-1 and KW10 will also work)
- 30cm of wire, AWG22 or similar
- 2 M2x10mm self-tapping screws
- 5x 6mm diameter x 3mm height magnets
- 2x M3x18mm/M3x20mm screws

# Build Process

## Probe assembly

For the probe assembly you need the following parts:

- [ ] 1x microswitch
- [ ] 2x M2x10 mm self tapping
- [ ] 4x 6 mm x 3 mm magnets
- [ ] 1.5mm Drill (optional)
- [ ] Multimeter to check for Continuity 
- [ ] Super Glue



Maybe you need to clear the holes for the microswitch, a 1.5mm drill bit should work fine.

Install the microswitch so that the arrow on the probe body is pointing to the little switch.





Then take your self tapping screws and screw the microswitch in place.



**Notice, there is an alternative method to install the magnets, that seems to improve fitting and results please read the instruction until the end and then decide on what is the bet method for you,**

Before placing the magnets, use some super glue on the holes (not a lot, just a drop), avoid the switch parts.

You want to install the magnets in the way that the ones which are connected to the microswitch, have the same polarity  The 3rd magnet should have the inverse polarity, you can use the included pressfit helpers to help in securing the probe when you are inserting the magnets.

There is no need for soldering, the probe microswitch connectors are press-fit on the magnets, they should remain with the top above the probe plastic.



Don't forget to install the magnet which holds the probe to the probe dock, make sure it is fully inserted.

As the last step of the probe assembly check if you have continuity between these two magnets



If you have a normally closed switch (as you should), then you should have a current flow, so continuity is established. When you press the switch you should lose continuity. When you have a normally open switch then the behavior is the other way around.

## AB/SB Mount Assembly

For the AB/SB Mount assembly you need the following parts

- [ ] 3x 6 mm x 3 mm magnets
- [ ] 2 x 18cm 22AWG cable to connect the Klicky Probe to the Microfit Terminal (if it turn out it's too big, can always cut to lenght)
- [ ] Multimeter to check for Continuity 
- [ ] Super Glue

The probe mount wires are also connected with pressure from the magnets, you can use the probe magnets as a template to insert the probe mount magnets, it is easier that way, so that the magnets are not inserted the wrong way.

|  |  |  |  |  |
| :---: | :---: | :---: | :---: | :---: |

You will not lose Y travel on any configuration in the tests that were done.

After everything is assembled let's check again for continuity.



### Press-fit the magnets

You can now press fit the magnets in place:

<p float="left">
  
  
</p>

Insert the AB mount and probe in the helper parts and you can then press fit with a vice or on a hard surface.

<p float="left">
  
  
  
</p>

### Alternative installation method (by [kyleisah](https://github.com/kyleisah) and [DrachenKatze](https://github.com/DrachenKatze)  (who came up with the idea)

- Insert switch into probe and install screws
- Install stripped wire leads into probe mount
- Apply dabs of glue to probe, and quarter-install 2 magnets into each hole, making sure to invert the polarity for the rear probe magnet hole
- Apply dabs of glue to the probe mount and line up the magnets from  the probe to the magnet holes of the mount and press them in best you  can so they stay in the holes
- Using the press fit tools, force the probe and mount together so they bottom out against each other.
- Do not pull the probe and mount apart, slide them apart and allow the glue to cure.
- After the glue has sufficiently cured (read the label) slide the  mount and probe back together so the magnets realign and check for  continuity at the ends of the probe leads.

## Final thoughts

For the installation, you should now install the dock (according with your printer instructions) and mount the probe mount.

It is working very well for me. If you decide to use it, please send me feedback, either here, or on Voron discord. My discord username is `@JosAr#0517`.

By standing on the shoulders of giants, let's see if we can see further.

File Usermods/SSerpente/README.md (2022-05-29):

This a collection with all the necessary printed parts to put Klicky probe on VzBot . 
My only personal contribution is the probe dock mount that i made to fit VzBot , all the other parts are not my creation .
I made the probe dock mount with press fit m3 nuts instead of heat inserts used in the original klicky design. 
In case of collision on z axis between the dock and the probe i added 2 more versions : one with z offset of the probe dock mount 1 mm lower and one 1 mm higher .

Klicky probe is a cheap and more precise alternative to various probe sensors (BlTouch, 3dTouch, inductive/capacitive sensors ) , and tested by me a standard deviation of 0.00065 
There are 4 parts needed : probe mount , probe (various probe lengths and even a switch extender if needed can be found on the klicky github) , probe dock and probe dock mount. 
 Inside the pictures folder i will put the print orientation. For the print settings i use a 0.2 layer height, 3 walls,5 top/bottom and 35% infill.

All the credits go to klicky probe creator and obvious to VzBot creators.
Link to VzBot : https://github.com/VzBoT3D/VzBoT-Vz330

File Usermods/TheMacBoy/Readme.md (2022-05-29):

---
title: TheMacBoy's Klicky Probe mount for EVA and Ender 5 Plus (with rails) compatibility
---

> Created by: [TheMacBoy](https://github.com/themacboy)

## Description
This is a modification of Klicky probe to be used in the EVA carriage, plus support arm for Ender 5 Plus with rails.

Klicky probe right

Klicky probe left

Klicky probe bottom

Klicky probe inside

Klicky probe

Ender 5 Plus support arm front

Ender 5 Plus support arm

## Compatible EVA version
2.2.0 - ?

## Related EVA parts
universal_face

## Source Klicky probe files
[Klicky Probe](../../Probes/KlickyProbes/STL)

## Source OnShape files
[Klicky mount for Eva ](https://cad.onshape.com/documents/2fc54d83c144f64dfbd5b70d/w/5a27aacdedad8aa85274c7e9/e/03e92f0ea05a500c94d12e60)

## Source FreeCad files
Ender-5 Plus arm support inside cad folder

## Changelog
v0.5 30/12/2021 TheMacBoy Release

v0.6 09/01/2022 Klicky probe modified the back size of the frame support, new version v.2

16/02/2022 Added my custom "klicky-variables.cfg" macro as example (my custom settings on my custom Ender-5 Plus ;)

## BOM Parts:
| No | Qty | Name | Printable |
| -- | --- | --- | --- |
| 1  | 1 | Eva-2.2 Klicky probe mount | [Yes](EVA_2.2^/stl/eva-2.2-klicky_probe_mount.stl) |
| 1  | 1 | Ender-5 Plus support arm v.1 | [Yes](Ender-5_(pro,plus)/stl/ender_5_plus-arm_v.1-body.stl) |
| 1  | 1 | Ender-5 Plus support arm v.2 | [Yes](Ender-5_(pro,plus)/stl/ender_5_plus-arm_v.2-body.stl) |

## STEP format:
| No | Qty | Name | Printable |
| -- | --- | --- | --- |
| 1  | 1 | Eva-2.2 Klicky probe mount | [Yes](EVA_2.2^/cad/eva-2.2-klicky_probe_mount.step) |
| 1  | 1 | Ender-5 Plus support arm v.1 | [Yes](Ender-5_(pro,plus)/cad/ender_5_plus-arm_v.1-body.step) |
| 1  | 1 | Ender-5 Plus support arm v.2 | [Yes](Ender-5_(pro,plus)/cad/ender_5_plus-arm_v.2-body.step) |

## BOM screws:
| Qty | Name | Observations |
| --- | --- | --- |
| 2 | M3 20mm | (hex head) |
| 1 | M4 20mm | (countersunk head) |
| 1 | M4 10mm | (countersunk head) |
| 2 | M4 T-Nut | |
| 2 | M3 12mm | (hex head) |
| 2 | M3 nuts | |
| 2 | M2 10mm | carpentry type |
| 2 | M3 inserts x D5 x L5 | |

## Hardware Required 
Standard EVA

Ender-5 Plus

## To Do 
pending to draw arm on OnShape

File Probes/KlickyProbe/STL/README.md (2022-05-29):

# STL files for common parts for Klicky probe



Here you can find the parts that are common across all printers-

There is no need for supports, all the files are ready to print, they are in the recommended orientation, the standard probe (KlickyProbe_v2.stl) can also be printed with the magnet hole facing down without supports.
You can also use brim on the probes to help with bed adhesion.

- Version 0.1 - initial release
- Version 0.2 - Revised probe and dock to improve the docking fit, remaining components are compatible
  - Thanks to oc_geek for improving the probing of a badly tilted gantry (10º) and the probe and dock attachment, it's much better now
- Version 2
  - Reduced the dock by 2mm, extended the dock mounts by 2mm
  - Added two new probes, one mostly for Voron v0 the oher for Tiny-M, they extend the original by different lengths below the nozzle

The Klicky Probe consists on four different components:
- Toolhead mount, found on the printer specific STL directory
- the probe itself
- probe dock
- Frame dock mount, found on the printer specific STL directory

The recommended printing configuration are:

* initial layer height:0.24mm
* layer height: 0.2mm
* bottom/top/perimeters: 4
* infill: more than 23%
* infill type: Cubic
* Thin walls: On

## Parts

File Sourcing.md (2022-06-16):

# Trusted suppliers

The following shops are all responsive and helpful, they can help with the sourcing of the required parts for your klicky probe.

| **Shop** |  **Location** | Hadware Kits | Parts | Klicky printed parts | Comments |
| --- | :---: | :---: | :---: | :---: | --- |
| [Fabrekko](https://www.fabreeko.com) | :us: | :heavy_check_mark: | some | :x: | lots of parts to expand 3d printers |
| [Lab4450](https://lab4450.com/) | :eu: :portugal: | :heavy_check_mark: | :x: |  :heavy_check_mark:  | kits for V0, V2, VT, Switchwire, Vcore, PCB's |
| [Vonwange](https://vonwange.com/) | :eu: :de: | :heavy_check_mark: | :heavy_check_mark: |  :heavy_check_mark:  | lots of parts to expand 3d printers |
| [Replimat](https://www.replimat.eu)  | :eu: :de: | :heavy_check_mark: | :heavy_check_mark: | :x: | specializes in some hard to find items |
| [KB-3D](https://kb-3d.com) | :us: | :heavy_check_mark: | :heavy_check_mark: | :x: | specializes in Open source community builds and parts|

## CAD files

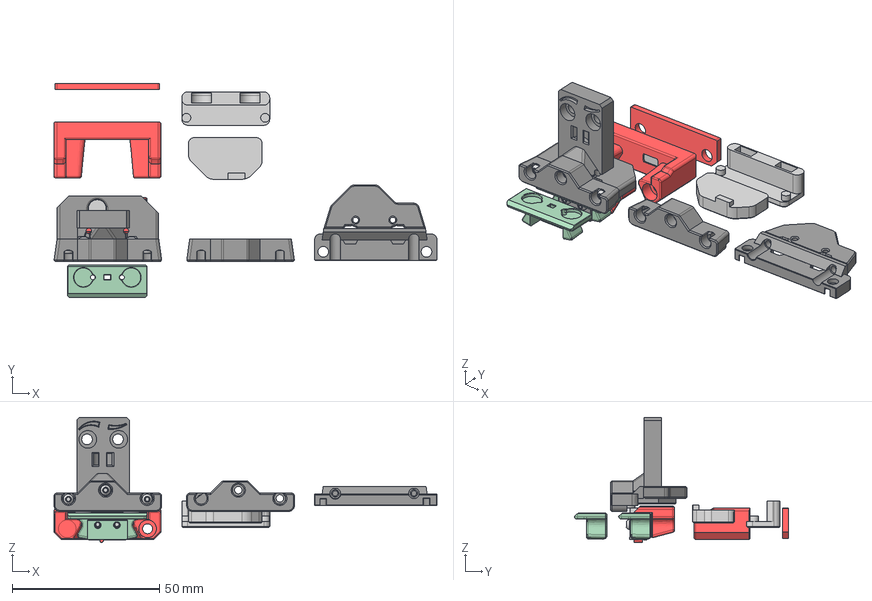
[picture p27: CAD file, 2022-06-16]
CAD/KlickyNGProbe v5.step
129.9 x 72.6 x 42.5 mm
M2x10 Self-tapping Screw (1)
Magnets (1)
D2F_ACTUATOR (1)
D2F_BASE (1)
Magnets
M2x10 Self-tapping Screw
Magnets (2)
KlickyNG_Probe_Helper_mount
KlickyNG_Probe_Helper_probe
2mm extender
Tiny-M

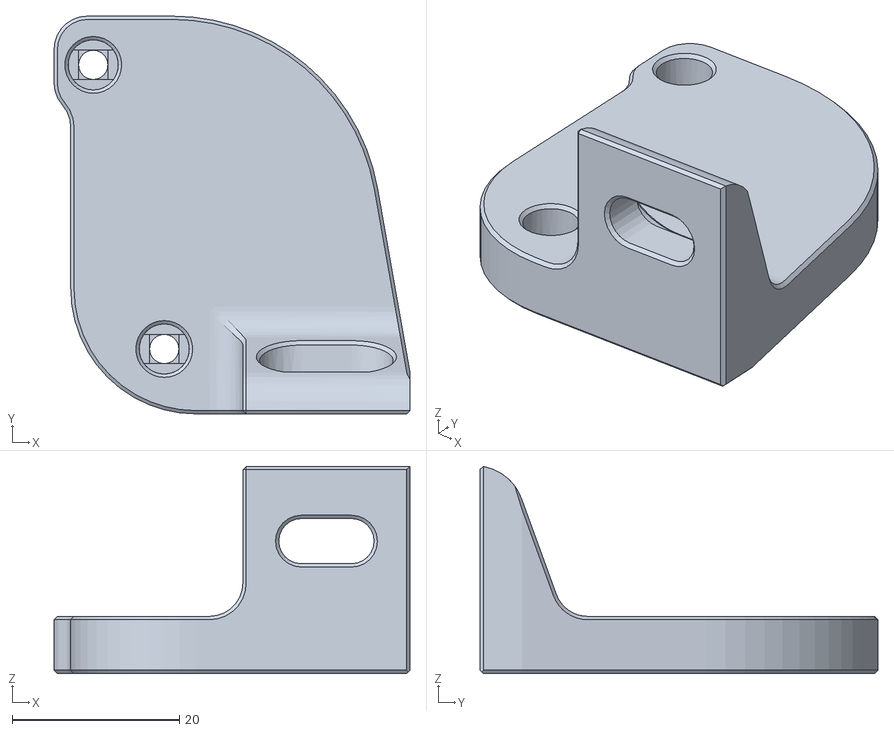
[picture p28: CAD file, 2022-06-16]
Printers/Voron/Switchwire/SW_STL/Servo_Mount_Body_right.stl
42.6 x 47.6 x 24.8

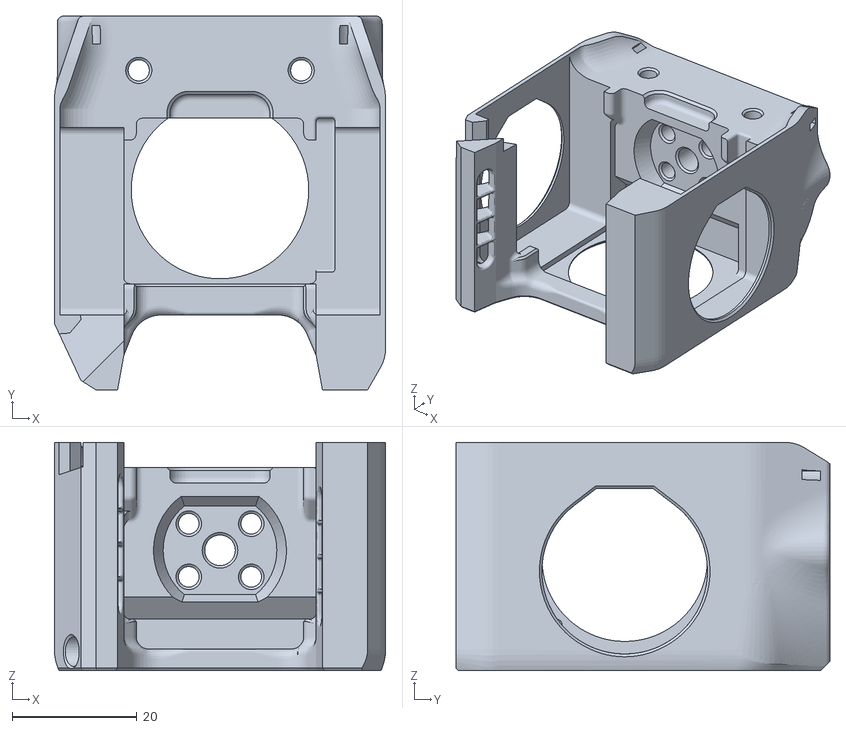
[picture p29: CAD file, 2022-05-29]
Printers/Voron/v0/v0_STL/Sherpa_VoronRevo_Cowling_wKlicky.stl
53.0 x 59.9 x 36.5

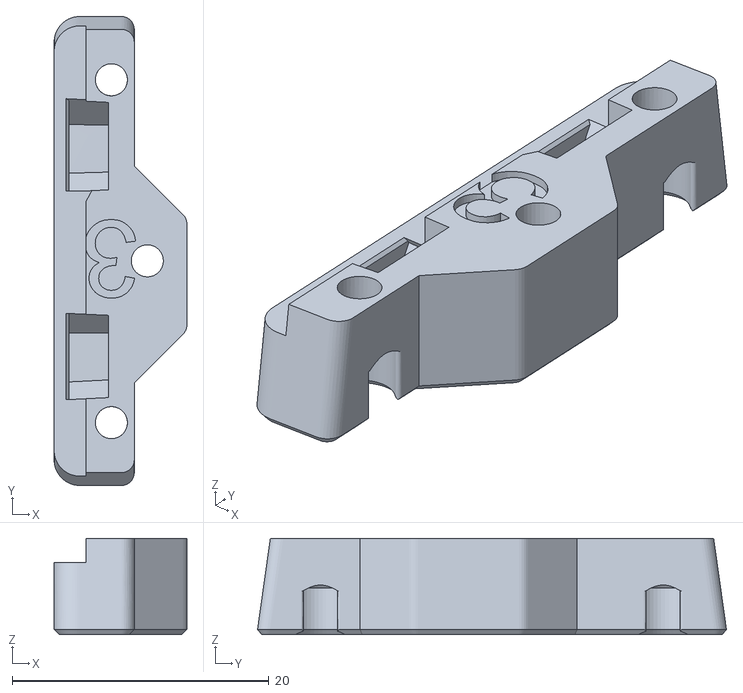
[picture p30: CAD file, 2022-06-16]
Probes/KlickyNG/STL/KlickyNG_ABSB_mount_3mm_front.stl
10.4 x 36.5 x 7.50

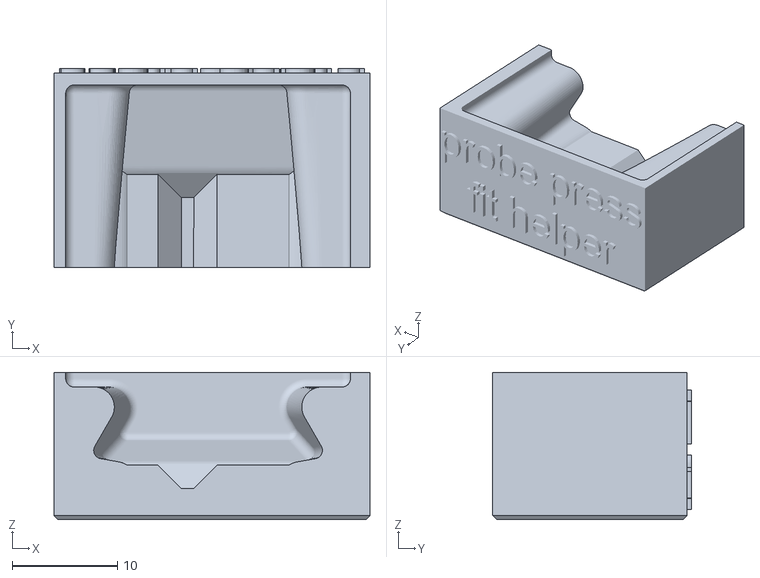
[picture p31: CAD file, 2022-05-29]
Probes/KlickyProbe/STL/Probe_pressfit_holder.stl
30.0 x 18.9 x 14.0

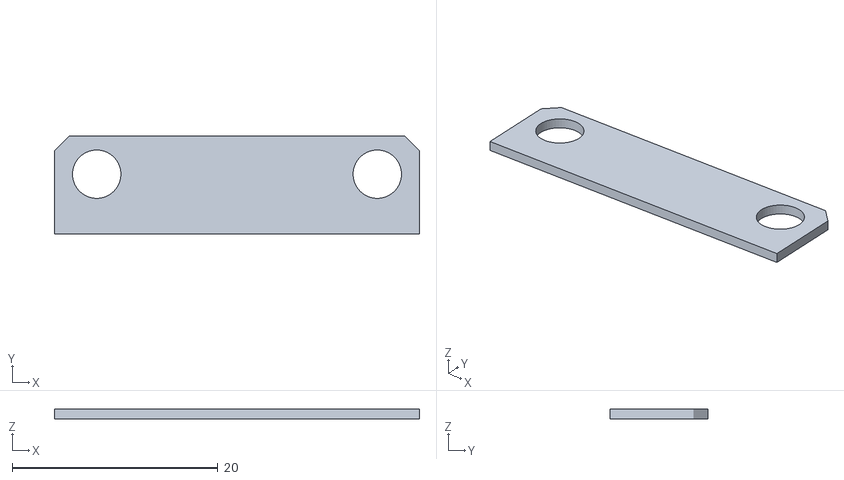
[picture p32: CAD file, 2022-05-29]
Probes/Unklicky/STL/1mm_Spacer.stl
35.5 x 9.50 x 1.00

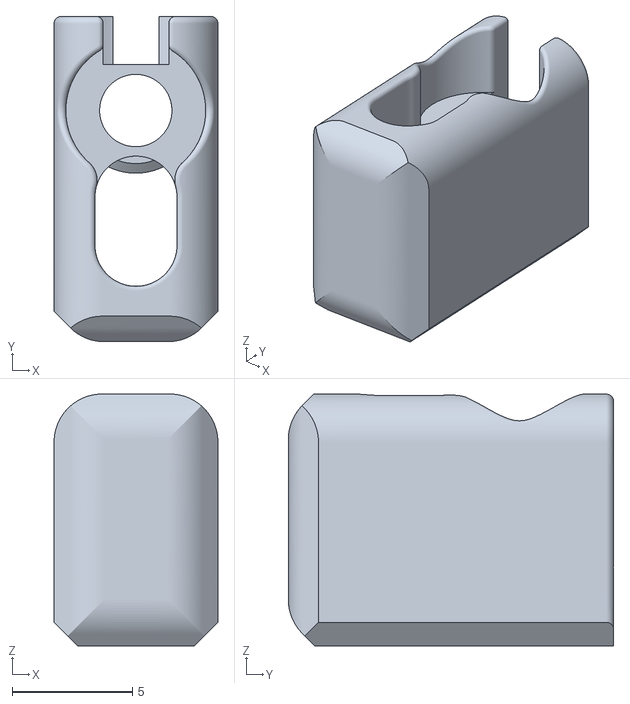
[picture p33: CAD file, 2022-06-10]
Probes/UnklickyNG MFP/STL/pin.stl
6.80 x 13.5 x 10.5

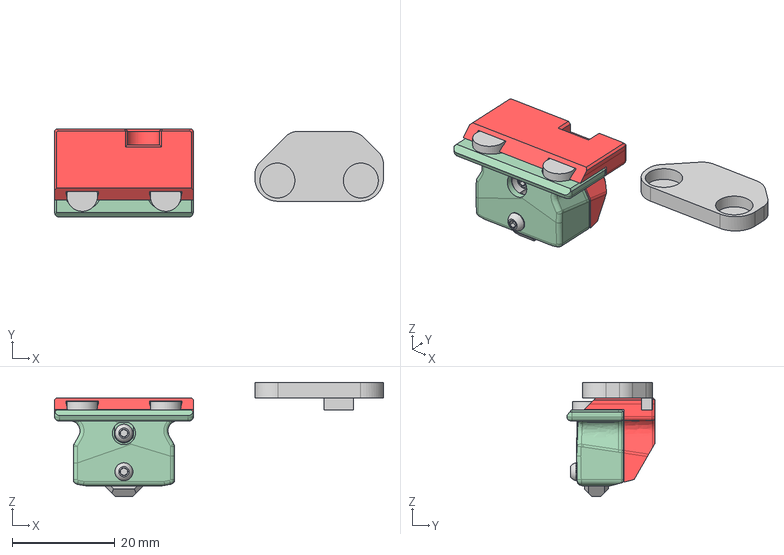
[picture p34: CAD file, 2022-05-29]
Probes/UnklickyNG/CAD/UnklickyNG_Probe.step
64.0 x 17.2 x 22.3 mm
M2x8 Self-tapping Screw (1)
UnklickyNG Helper

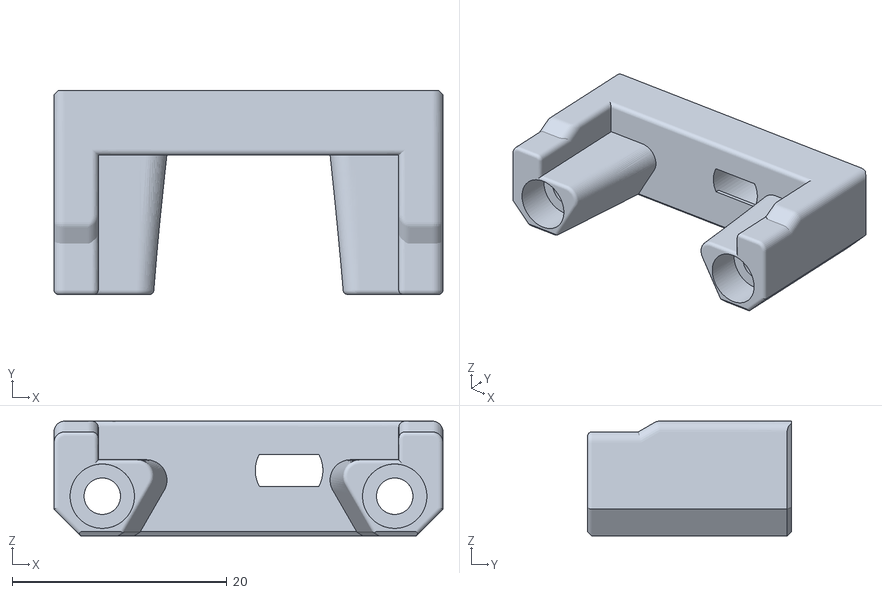
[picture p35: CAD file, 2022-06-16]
Probes/UnklickyNG/STL/KlcikyNG_Probe_Dock.stl
36.3 x 19.0 x 10.7

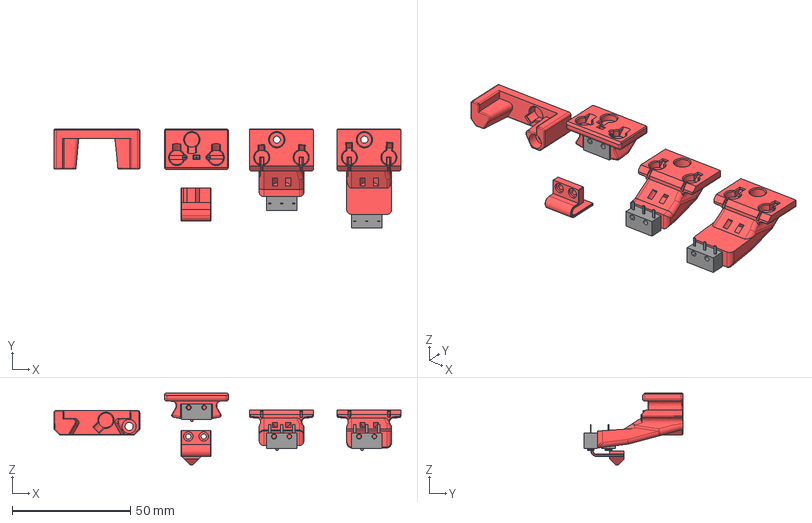
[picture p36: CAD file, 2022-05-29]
Usermods/SSerpente/Cad/Klicky Probe + Dock.step
146.6 x 41.9 x 30.3 mm
D2F_ACTUATOR
D2F_BASE
D2F_ACTUATOR (3) (1)
D2F_BASE (3) (1)
D2F_ACTUATOR (2)
D2F_BASE (2)
Probe Dock v2
Switch_extender

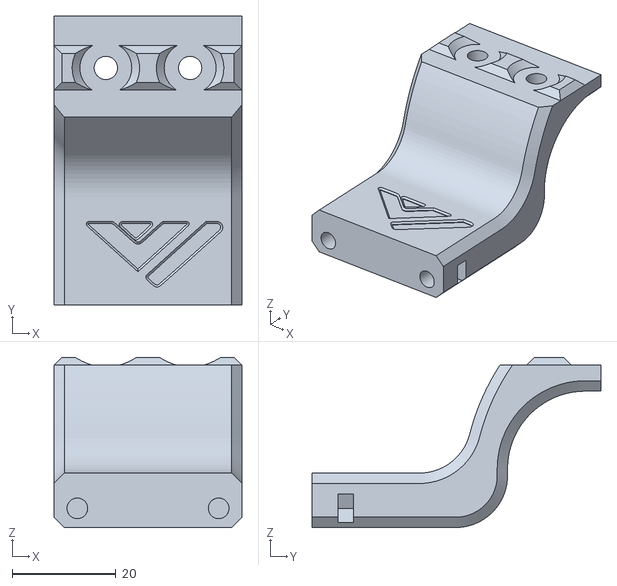
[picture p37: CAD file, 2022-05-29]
Usermods/SSerpente/Stl/Klicky dock probe VzBot v1.stl
36.3 x 55.7 x 32.8

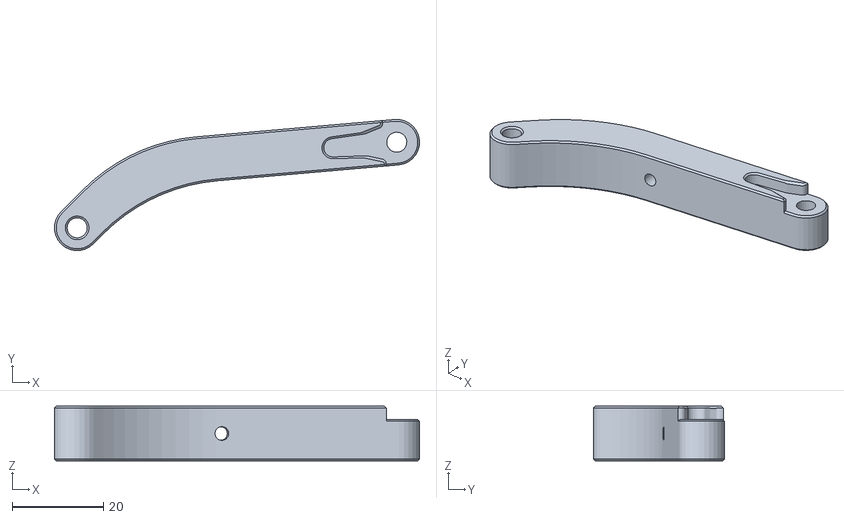
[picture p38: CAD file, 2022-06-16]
Printers/Voron/Switchwire/SW_STL/Drive_arm_front.stl
80.0 x 28.7 x 12.0

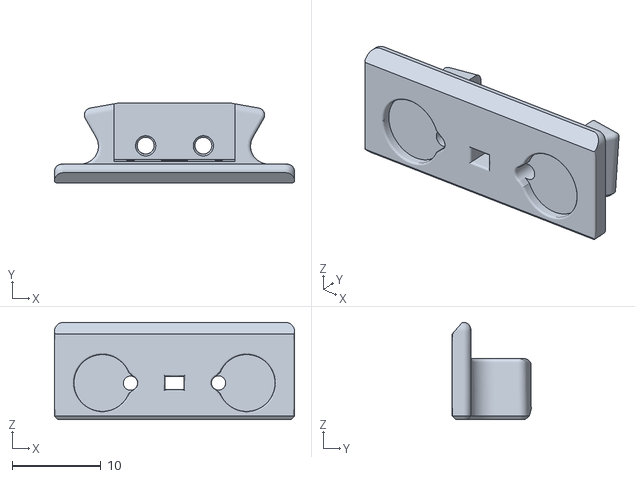
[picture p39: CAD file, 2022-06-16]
Probes/KlickyNG/STL/KlickyNG_Probe_insert.stl
27.0 x 8.97 x 10.9

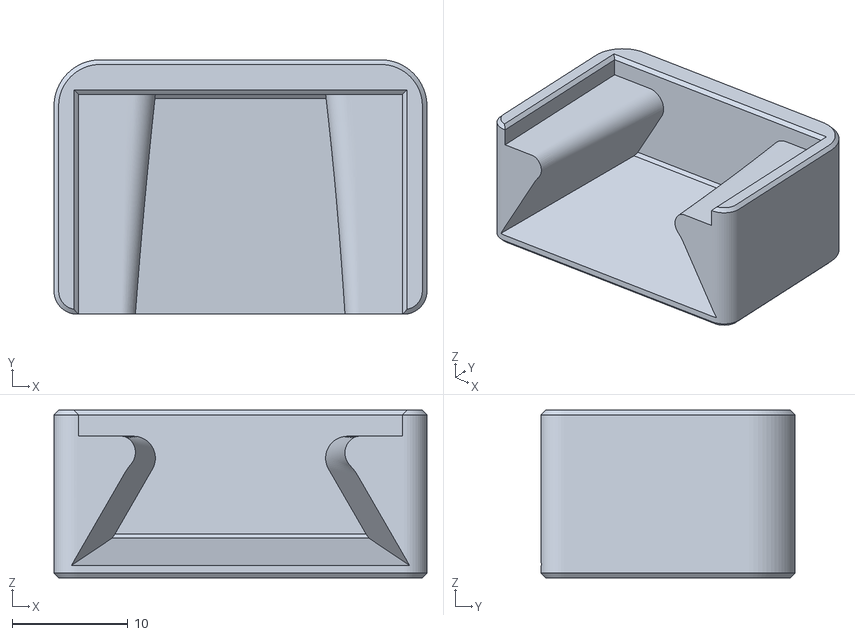
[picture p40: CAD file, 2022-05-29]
Probes/KlickyProbe/STL/Longer_probe_pressfit_helper.stl
32.3 x 22.0 x 14.5

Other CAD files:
Probes/Unklicky/STL/Probe_Dock_v2.1.stl
Probes/UnklickyNG MFP/STL/cap.stl
Probes/UnklickyNG/STL/KlickyNG_ABSB_mount_3mm_front.stl
Usermods/SSerpente/Cad/Klicky probe dock VzBot.step
CAD/KlickyNGProbe_v3.step
Printers/Voron/Switchwire/SW_STL/2mm_extender.stl
Printers/Voron/Switchwire/SW_STL/Drive_arm_back.stl
Printers/Voron/Switchwire/SW_STL/Servo_Mount_Body_center.stl
Printers/Voron/Switchwire/SW_STL/Servo_Mount_Body_left.stl
Printers/Voron/Switchwire/SW_STL/Servo_dock_mount_left.stl
Printers/Voron/Switchwire/SW_STL/Servo_dock_mount_right.stl
Printers/Voron/v1.8_v2.4_Legacy_Trident/Usermods/Minsekt/MGN12H_native_mantis_KlickyNG_xcarriage/CAD/Mantis_MGN12_KlickyNG_including_dock v6.step
Printers/Voron/v1.8_v2.4_Legacy_Trident/Usermods/Minsekt/MGN12H_native_mantis_KlickyNG_xcarriage/STL/NGclamp.stl
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

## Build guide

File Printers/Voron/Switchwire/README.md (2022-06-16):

# Klicky Probe for  Vorondesign Switchwire printers

Here you will find the necessary files and documentation to print and setup your own klicky probe on the Switchwire (finally).

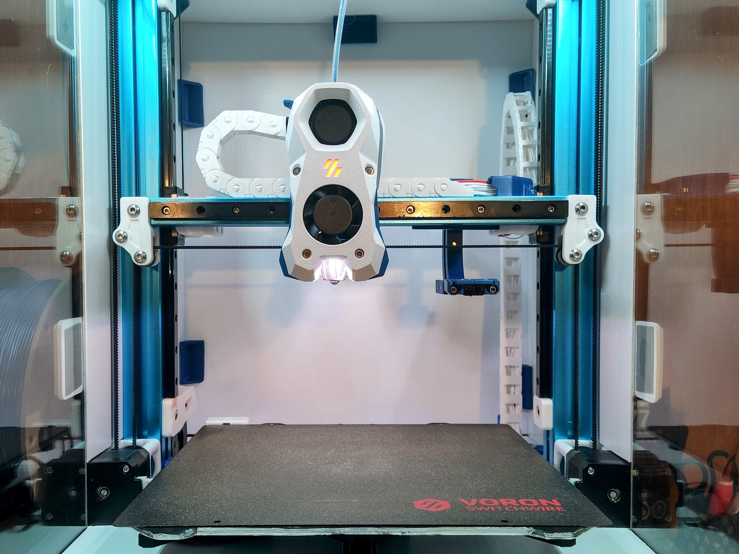
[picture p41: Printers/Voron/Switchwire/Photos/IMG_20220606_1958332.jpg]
Switchwire Klicky


It uses a slightly different approach than most magnetically attached probes, it's secured on the X extrusion, so it's available on any Z height and can be used without knowing the Z position, just like all the others.

I do not own a  Switchwire, so the tests were made with the help of the Voron community to whom i would like to thanks for the support, first and foremost to Patrice who was an excelent contributor to the project and main instigator, and also marciorssilva, Iconic FAB lv and Jason who tested and troubleshooted several components.

This directory has the STL files properly oriented for printing and community mods for the respective printer, there are [klipper](../../../Klipper_macros) macros and [RRF](../../../RRF_macros) macros on the repository.

You can find more information about the Voron printers at the [website](https://vorondesign.com/) or go check the [discord](https://discord.gg/voron), for the record, i own a v2.4, this is how i would describe them "A Voron is a fast high quality printer, i print with much better quality  the perimeters at the draft speed of my old bedslinger. It also has a  big community with lots of documentation and new ideas."

It has a servo powered dock on the X axis, the bed can be fully used during printing, and it can also be used without extra configurations as a virtual Z endstop.

Above all, have fun and be excellent to one another, now to the instructions.

This mod is not yet on [VoronUsers repository](https://github.com/VoronDesign/VoronUsers/tree/master/printer_mods/JosAr/Klicky-Probe), should be soon. 

They say an image is worth a 1000 words, but this is better described by a [small movie](https://youtu.be/if7qnrqHi_w), this was filmed by Patrice.

Some picture before heading to bussiness.

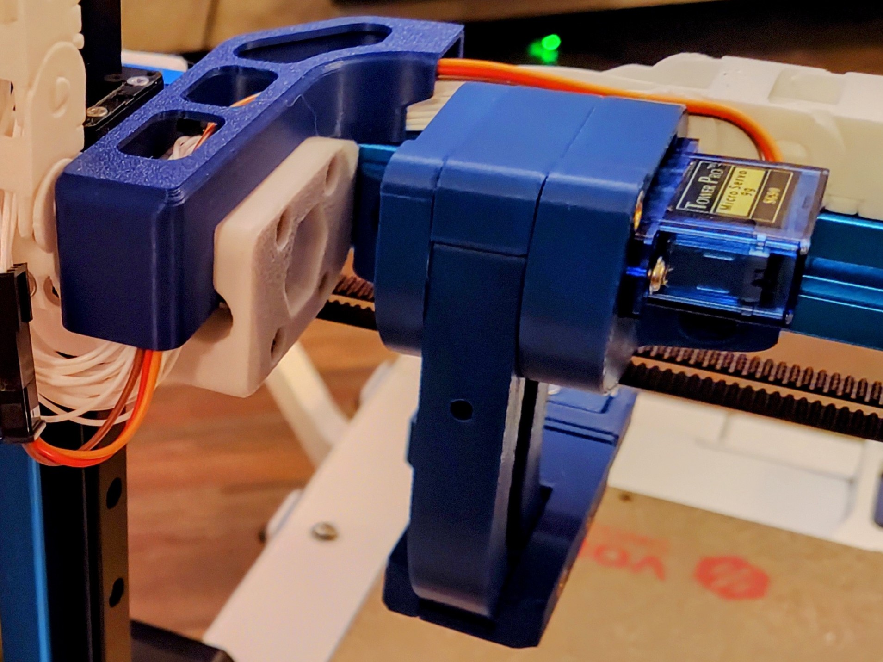
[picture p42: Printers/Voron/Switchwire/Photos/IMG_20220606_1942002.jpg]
backview
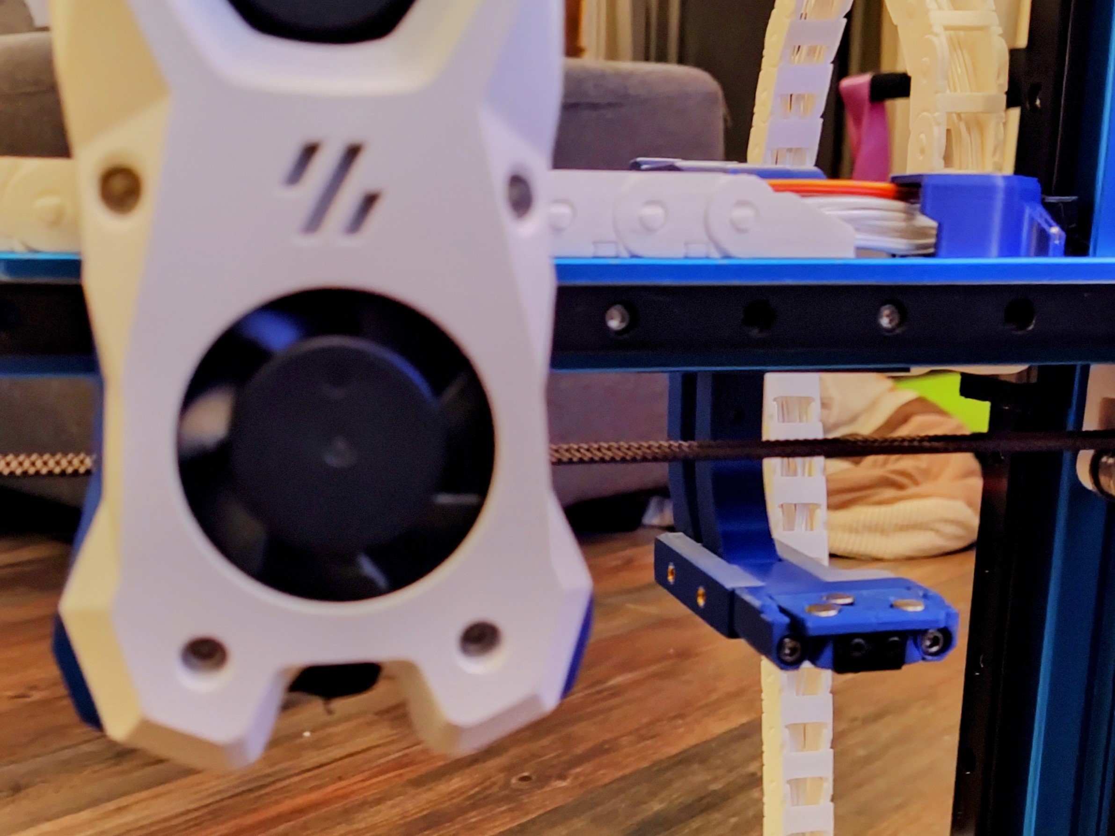
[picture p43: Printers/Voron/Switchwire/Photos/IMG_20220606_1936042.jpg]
sw_frontview
|  |  |
| --- | --- |

## Probe selection

Right now, there are two probe attachment options, each with two probe types.

### [Regular Klicky](../../../Probes/KlickyProbe/)

First klicky probe, based on the [Quickdraw probe](https://github.com/Annex-Engineering/Quickdraw_Probe), with an added third magnet for added stability and fixed dock gantry setups.

klickyprobe

It uses magnets to secure the probe to the mount and also to make the electrical connection.
The magnets can be glued to prevent them from coming loose.
It supports a microswitch probe and Unklicky ([invented by DustinSpeed](https://github.com/majarspeed/Unklicky)) (self built probe, that so far surpasses the microswitches in common use) based probing.

To assemble this probe, choose one and head to the assembly instruction below, the probe BOM is also there:

- [KlickyProbe](../../../Probes/KlickyProbe/)
- [Unklicky original (coiled wire variant, uses one 3x2 magnet)](https://github.com/majarspeed/Unklicky/tree/main/Unklicky)
- [Unklicky BFP-HS (heat set version, uses only 6x3 magnets)](https://github.com/majarspeed/Unklicky/tree/main/BFP-HS), should be more resilient over time
- [Unklicky BFP (coiled wire variant, uses only 6x3 magnets)](../../../Probes/Unklicky/)

### [KlickyNG](../../../Probes/KlickyNG/)

New enclosed magnets probe, it does not require glue to help prevent the magnets from coming loose, magnets are also self aligning.
This approach only uses common and easy to source parts.

klickyNGprobe

Also supports a microswitch probe and Unklicky ([invented by DustinSpeed](https://github.com/majarspeed/Unklicky)) (self built probe, that so far surpasses the microswitches in common use) based probing.

To assemble this probe, choose one and head to the assembly instruction below, the probe BOM is also there:

- [KlickyNG Probe](../../../Probes/KlickyNG/)
- [UnklickyNG original (coiled wire variant, uses two 3x2 (or 3x4) magnets)](../../../Probes/UnklickyNG/)
- [UnklickyNG BFP (coiled wire variant, uses only 6x3 magnets)](../../../Probes/UnklickyNG/)

## Bill of Materials (BOM)

### Tools:

- Multimeter to check for Continuity 
- Super Glue (optional)
- Soldering Iron to install the heat inserts

### Probe:

- check the links on the probe section above

### AB/SB mount:

- check the links on the probe section above

### Probe dock:

- check the links on the probe section above

### Servo mount

- 2x M3x24 mm SHC Screws
- 3x 1m 24AWG cable to connect the servo 
- 2x  threaded insert M3x5 mmx4 mm
- 2x M5x10 BHCS
- 2x M5 T-Nut for 2020 extrusion
- 1x MG90s servo with arms and mounting screws included

### Arms

- 4x 6 mm x 3 mm magnets (N35 recommended)
- 3x20 mm PTFE Tube (4mm OD 2mm ID) 
- 1x12 mm PTFE Tube (4mm OD 2mm ID) 

### Dock mount:

- 2x M3x20 mm SHC Screws
- 4x  threaded insert M3x5 mmx4 mm

## Sourcing

To get the best experience, please consider purchasing from the trusted list of suppliers bellow.

[trusted suppliers list](../../../Sourcing.md)

## Parts location

The probe STL's are located on each probe directory on the STL

The printer specific STL's are located [here](./SW_STL).

The CAD with all the parts are [here](../../../CAD).

## What to print

### Probe

follow the instructions on the Probe selection section

### AB/SB mount

follow the instructions on the Probe selection section

### Probe dock

follow the instructions on the Probe selection section

### Servo mount

- Servo_Mount_Body_right
- Servo_Mount_Body_center
- Servo_Mount_Body_left

### Arms 

- Drive_arm_front
- Drive_arm_back

### Dock mount

- Servo_dock_mount_right
- Servo_dock_mount_left
- 2x 2mm_extender (might be required)

### Printing instructions

Recommended printing settings:

* initial layer height:0,24
* layer height: 0.2mm
* bottom/top/perimeters: 4
* infill: more than 23%
* infill type: Cubic
* Thin walls: On

The recommended printing orientation is (the STL's are correctly oriented for printing):

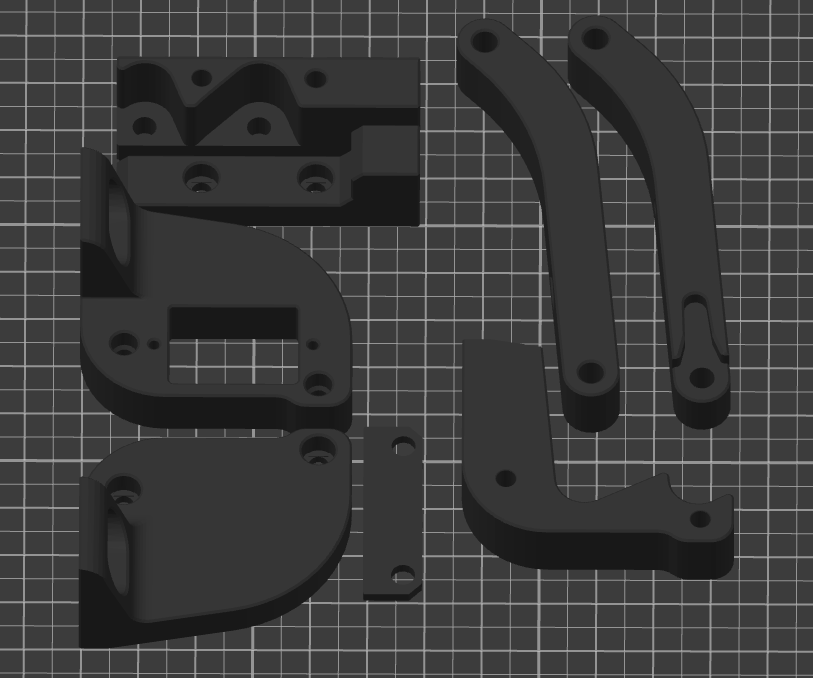
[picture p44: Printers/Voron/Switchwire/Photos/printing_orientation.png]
printing orientation


It was tested and printed with ABS, might work on other materials, if you try, let me know how it worked out.

### Components

Klicky Switchwire parts

## Assembly

### Step 1 - Servo arm preparation

Find the servo arm that fits the dock arm the best and cut off anything else on that arm if there is anything, tipically is the one that is circled.

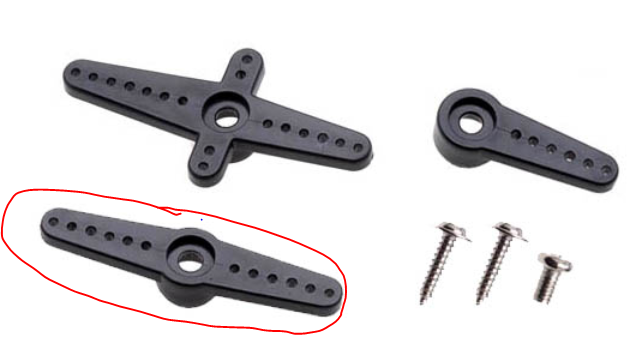
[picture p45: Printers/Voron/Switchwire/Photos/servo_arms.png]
servo_arms


servo_arms_cut

### Step 2 - Arms preparation

Insert 2 6x3 magnets on each arm socket.

Switchwire arms

Also insert the 3 20mm PTFE tubes and the 12 mm one on the arms as displayed on the picture:

Switchwire arms

### Step 3 - Dock mount

With the soldering iron tip, heat set the 4 threaded inserts like you did within your Voron build on the dock mount body, two on the top of each body and two on the side of the Servo_dock_mount_left:

| dock_mount1.1 | dock_mount1.2 |
| ---: | :--- |

Now attach the arms with the 20mm PTFE tube on the Servo_dock_mount_left part, take care to match the arms positions as they are on the image:

dock_mount2

Complete assembly by attaching the Servo_dock_mount_right and secure with 2x20 mm m3 screws  :

dock_mount3

### Step 4 - Servo mount

With the soldering iron tip, heat set the 2 threaded inserts like you did within your Voron build on the Servo_mount_body_left.

dock_mount2

Now attach the arms with the 20mm PTFE tube on the Servo_mount_body_right part, take care to match the arms positions as they are on the image:

dock_mount2

Insert the Servo_Mount_Body_center following the body contour:

dock_mount3

And complete assembly by attaching the Servo_Mount_Body_left and secure with 2x24 mm m3 screws:

dock_mount3

### Step 5 - Probe Dock assembly

Now attach the probe dock assembly that you want to use to the Dock arm with 2x16mm m3 screws.

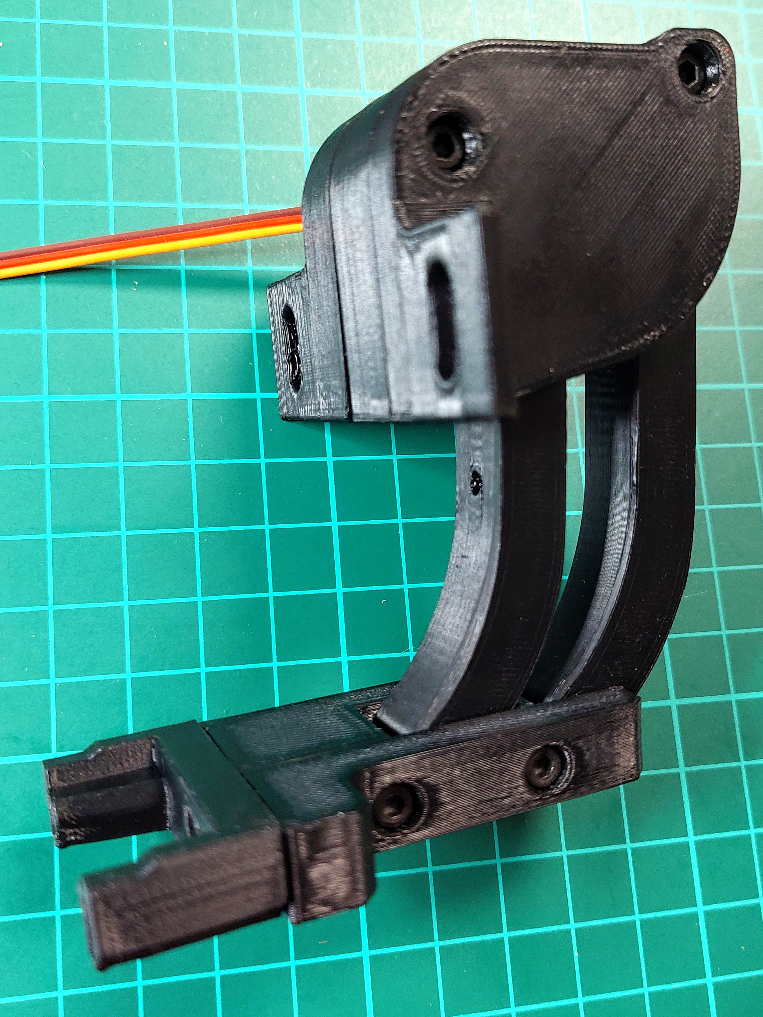
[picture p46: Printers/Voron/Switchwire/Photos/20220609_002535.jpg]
dock_mount4


Note: you may need to use later a dock extender to allow for easier probe docking and attaching.

### Step 6: Servo MCU configuration

To calibrate the servo, we will need to wire it temporarily to the MCU, you should use the same pins and configuration for the final setup, but for now the wires don't need to be very long, just long enough that you can work comfortably. 

The servo has 3 wires, as you can see from this picture:

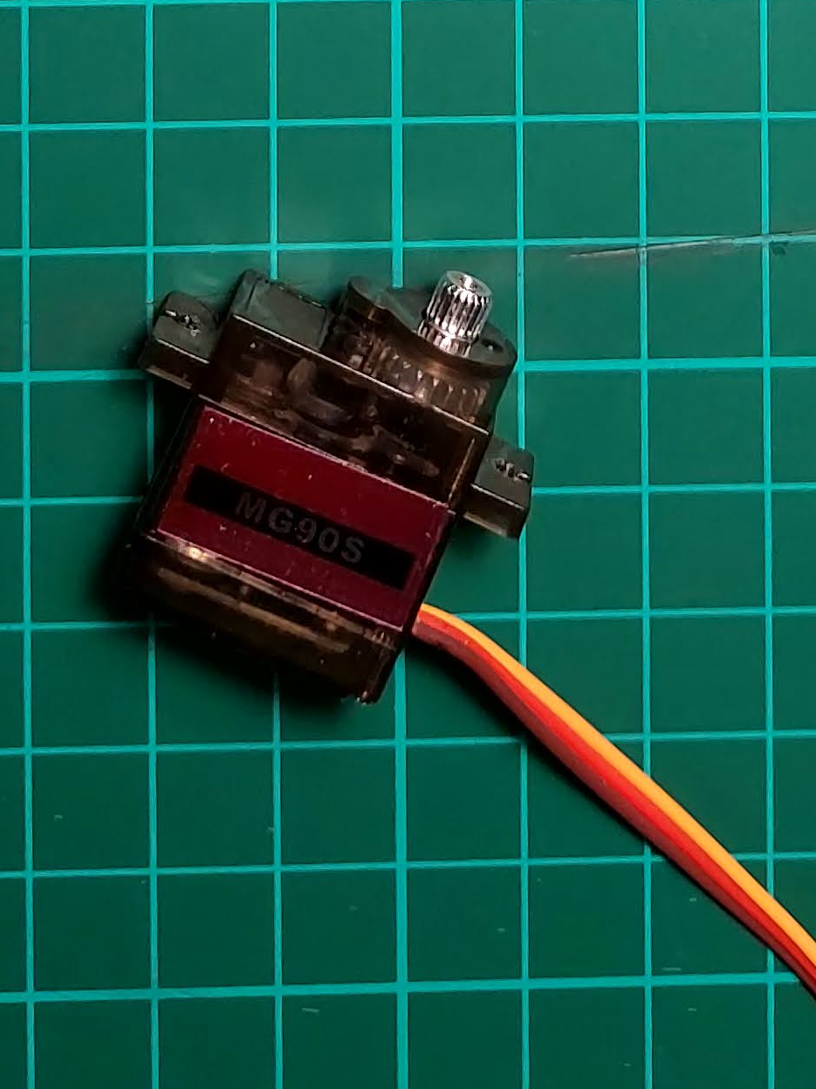
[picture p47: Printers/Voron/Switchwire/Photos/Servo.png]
servo


Normally, the GND is the brown, the red is the +5v and the orange is the PWM pin.

Servo diagram

The GND and PWM you wire to the MCU, on a SKR mini E3, you can use the PWR-DET or E0-STOP pins.

pins

The 5v, should be wired to the 5V PSU or to the same power supply of your raspberry pi, as the servo can use more power than the MCU 5v can supply.

The following klipper servo configuration should be added now to your printer.cfg, we will need it to calibrate the arms position. 

```python
[servo klicky_servo]
#check were your servo is wired
pin: PC12
maximum_servo_angle: 180
minimum_pulse_width: 0.00025
maximum_pulse_width: 0.0024

[gcode_macro _servo_test_angle]
gcode:
	{% set angle  = params.angle|int %}
	
    SET_SERVO SERVO=klicky_servo ANGLE={angle}
    G4 P1000
    SET_SERVO SERVO=klicky_servo WIDTH=0.0
```

restart klipper now, wire the servo and check if you can move it by issuing the following commands:

```python
_servo_test_angle angle=0
_servo_test_angle angle=90
```

Your servo should move more or less 90 degree between those two commands.

### Step 7: Servo calibration

The servo position needs to be reset, so that we can setup the angle easily.
Begin by issuing the instruction "_servo_test_angle angle=5" so that the servo will move to it's calibrated 5 degree position, then:

move the arms to the deploy position, like on the picture

servo

then attach the servo arm to it's place

servo

insert the servo on it's final place, attaching the arm to the servo pinion

servo

then remove the servo taking take that the arm is still attached to the pinion

servo

secure the arm with the included screw:

servo

and finally install the servo in its place and secure with the two included screws:

servo_installed

Test now with "_servo_test_angle angle=0" the arm should move fully to the deploy position, if it does not, you need to recheck the servo arm position, or decrease the angle, you can go until -90, remember that value.

Now, using the same macro, test the correct value for the arms to fully retract, start with the value above and add 10 or 5 degrees each time, preferably until the arm magnets touch one another.

Remember these values, you will need them later on klicky-variables configuration:

```python
variable_servo_deploy:          angle value with the arms on the deploy position
variable_servo_retract:         angle value with the arms on the retract position
```

### Step 8: Physical installation

- 2x M5x10 BHCS
- 2x M5 T-Nut for 2020 extrusion

The servo mount is mounted on the back of the X extrusion with two M5 T-Nuts, it has a M5 hole on each side of the servo mount that you secure to the extrusion.

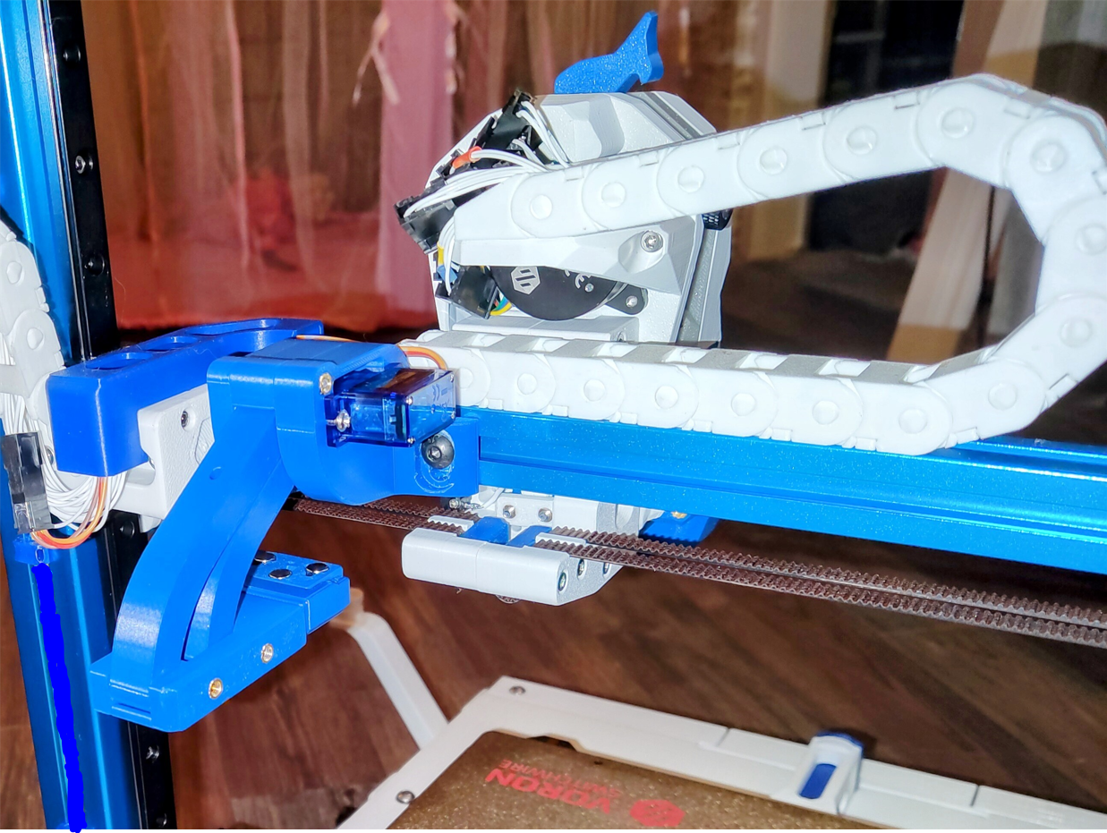
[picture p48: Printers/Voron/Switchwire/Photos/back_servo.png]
back_servo


Is is better to mount it near the Z cable chain so that the servo cable path is smaller and you can keep the stock servo cable, and just change the dupont end to a microfit or similar.

The servo mount is slightly adjustable on the Z, so you push the dock (with a probe) to the deploy position and attach the probe to the toolhead and then secure the servo dock in a position that can deliver the probe consistently to the toolhead mount.

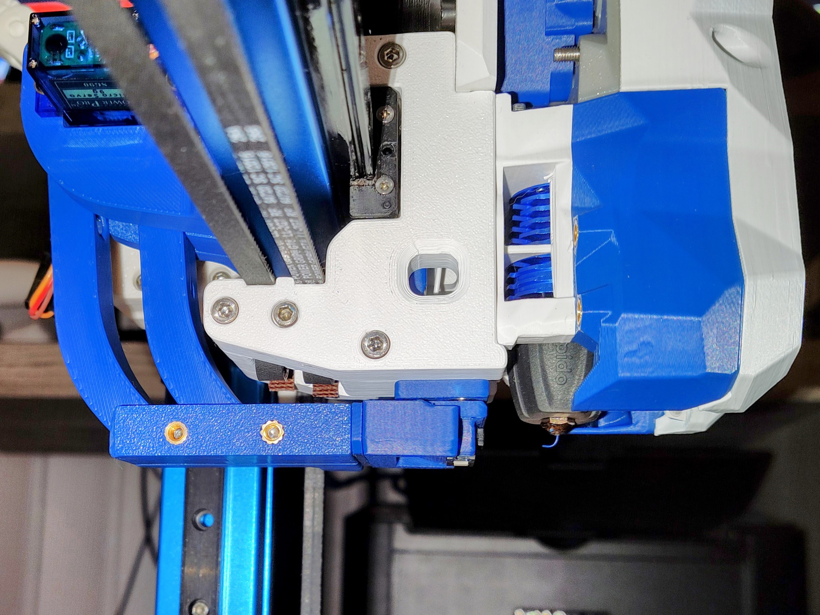
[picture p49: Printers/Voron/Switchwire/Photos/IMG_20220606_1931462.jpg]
servo_deployed


It should look like the image above when installed.

### Step 9: Servo Wiring on the chains

To wire the servo, it's recommended to use 3 new wires on the Z cable chain connected to a microfit or a JST female, that will connect to the servo cable like on the images bellow.

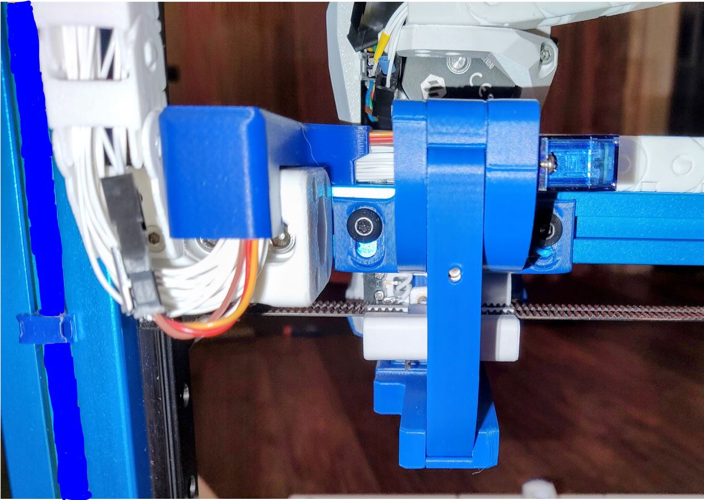
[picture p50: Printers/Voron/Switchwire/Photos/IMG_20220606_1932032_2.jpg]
wire_chains


Then connect and recheck the MCU connections and 5v PSU servo connections as you configured on step 6.

### Step 10: klipper configuration

Unfortunately, I do not know how to document RRF probe configuration, so here is only Klipper configurations.

As of right now, klipper and RRF have no inbuilt support for a removable probe, fortunately, it does support very robust macro programming, so you will need to add macros to be able to dock and attach the probe as necessary, as well as supporting the rest of the functions that require the usage of a probe.

The macros and instructions on how to configure are located on the [Macro directory](../../../Klipper_macros), you need to **check that before continuing on the build**, there are also some [RRF scripts](../../RRF_macros) that work for the Voron V2.4 and might work for the switchwire also.

For the Voron Switchwire, these are the recommended configuration on the klicky-variables.cfg:

```python
[gcode_macro _User_Variables]
variable_verbose:             True    # Enable verbose output
variable_debug:              False    # Enable Debug output
variable_travel_speed:         200    # how fast all other travel moves will be performed when running these macros
variable_move_accel:          1000    # how fast should the toolhead accelerate when moving
variable_dock_speed:            50    # how fast should the toolhead move when docking the probe for the final movement
variable_release_speed:         75    # how fast should the toolhead move to release the hold of the magnets after docking
variable_z_drop_speed:          20    # how fast the z will lower when moving to the z location to clear the probe

variable_safe_z:         	    25    # Minimum Z for attach/dock and homing functions
# if true it will move the bed away from the nozzle when Z is not homed
variable_enable_z_hop:        True    # set this to false for beds that fall significantly under gravity (almost to Z max)

variable_max_bed_y:            250    # maximum Bed size avoids doing a probe_accuracy outside the bed
variable_max_bed_x:            250    # maximum Bed size avoids doing a probe_accuracy outside the bed

# if a separate Z endstop switch is in
# use, specify the coordinates of the switch here (Voron).
# Set to 0 to have the probe move to center of bed
variable_z_endstop_x:            0
variable_z_endstop_y:            0

#Check the printer specific documentation on klipper Dock/Undock configuration, these are dummy values
#dock location 
variable_docklocation_x:      1000    # X Dock position
variable_docklocation_y:      1000    # Y Dock position
variable_docklocation_z:      -128    # Z dock position (-128 for a gantry/frame mount)

#The following variables are used if the dock is deployed and retracted via a servo motor
variable_enable_dock_servo:   True    # Set to true if your klicky dock is servo-controlled
variable_servo_name: 'klicky_servo'   # The name of the dock servo defined in printer.cfg under [servo]
variable_servo_deploy:          10    # angle value with the arms on the deploy position (found in step 7)
variable_servo_retract:         11    # angle value with the arms on the retract position (found in step 7)
variable_servo_delay:          250    # This is a delay to wait the servo to reach the requested position, be carefull with high values

#Dock move, final toolhead movement to release the probe on the dock
#it's a relative move
Variable_dockmove_x:           -40
Variable_dockmove_y:             0
Variable_dockmove_z:             0

#Attach move. final toolhead movement to attach the probe on the mount
#it's a relative move
Variable_attachmove_x:           0
Variable_attachmove_y:           0
Variable_attachmove_z:           0

```

This is probe configuration is with the default Switchwire SKR mini E3 v2 configuration, with the probe connected to the PC14 pin, please update it to your specific configuration:

```python
[probe]
Pin: ^PC2
x_offset: 0.0
y_offset: 19.75
z_offset: 6.17
speed: 5
lift_speed: 7
samples: 3
samples_result: median
sample_retract_dist: 2
samples_tolerance: 0.01
samples_tolerance_retries: 10
```

I recommend a probing speed between 3mm/s and 10mm/s, you may experiment to see what is the better speed for your machine.
Please confirm that if you are not using a endstop pin, that the pull-up is enable by using the ^ sign, normally the endstop pins have a hardware solution that does not require this configuration.
Depending on your switch you may need to add a `!` to invert that pin (normally open vs. normally closed).

**Remember that Switchwire uses the probe as the endstop, so you need to run probe_calibrate before printing**

### Step 11: klipper  Dock/Undock  configuration
#### Adjust Probe Pickup Position

One of the last things we need to do is to adjust the probe pickup position.

Home the X axis of your printer, then manually (with G0 X or GUI moves) move the toolhead until you can simulate with sucess the docking and attaching of the probe to the toolhead mount, use this value.

Open your `klicky-variables.cfg` and find the `#dock location` section and edit the following two line

```python
variable_docklocation_x: #what you found above
variable_docklocation_y:125 #middle of the bed
```

Test now with the ATTACH_PROBE and DOCK_PROBE if it docks and is removed correctly, some common points that can give problems are:

* the dock magnet is touching the back probe magnet, they cannot touch, push them further in
* the probe is hitting the dock arms, please move the toolhead more to the side where the probe does not hit, by 1mm at a time, until it works
* the probe is falling after being release, the dock is too far away, you can insert one or several 1mm spacer to move the dock and solve this
* the probe is not attaching to the mount, the dock is too far away, you can insert one or several 1mm spacer to move the dock and solve this

***WARNING when you are doing PROBE_ACCURACY, make sure that the probe is above the bed, the PROBE_ACCURACY macro does not move the toolhead in X or Y.***

Congratulations, your done :).

## Firsts tests

Before starting to test klicky, and from past mistakes, please use either the metal side of your PEI or your most damaged sheet and if possible, change your printer maximum speed, acceleration and Z current, on klipper with TMC steppers, you can do this:

```python
SET_TMC_CURRENT STEPPER=stepper_z CURRENT=0.2 
SET_VELOCITY_LIMIT ACCEL=1000
SET_VELOCITY_LIMIT VELOCITY=50
```

Enjoy your Klicky Probe!

It is working very well, if you decide to use it, give me feedback, either here, or on discord, my discord user is JosAr#0517.

By standing on the shoulders of giants, lets see if we can see further.

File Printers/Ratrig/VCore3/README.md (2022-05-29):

# Klicky Probe for Ratrig VCore3 printers

Here you will find the necessary files and documentation to print and setup your own klicky probe on the VCore3 

This directory has the STL files properly oriented for printing and community mods for the respective printer, there are [klipper](../../../Klipper_macros) macros and [RRF](../../../RRF_macros) macros on the repository.

You can find more information about the RatRig printers at the [website](https://www.ratrig.com/) or go check the [discord](https://discord.gg/bxqvFH4UzW). As the main developer of this modification variant for the VCore3 I own a custom shaped VCore3 printer. These parts have however been tested now with quite a few of the standard variations sold by Ratrig.

Due to the fact there is no area on the VCore3 where the dock can be fully outside the footprint of the print bed you will lose a small amount of print volume in the very front left corner... Note the default profile uses this area for the purge line anyway and this does not need to be modified as the direction of the purge line ensures the probe is not picked up.

Above all, have fun and be excellent to one another, now on to the instructions.

V2.4 Klicky Probe

## Mounting

### Probe dock mount

The probe dock is mounted to the front left extrusion, depending on your leadscrew length some of it may poke through the hole in the bracket

### Probe toolhead mount

The probe toolhead mount has been designed to be directly compatable with the EVA system and bolts onto the probe mounting holes. (Note it does however have a different probe offset to the standard bl touch and inductive probes)

## Bill of Materials (BOM)

### Tools:

- 1.5mm Drill (optional)
- Multimeter to check for Continuity 
- Super Glue (optional but advised)
- Soldering Iron

### Probe:

- 1x microswitch (the omron D2F-5 or D2F-5L (removing the lever is required), other also work with reduced accuracy or repeatability (mostly anecdotal evidence, needs a proper sudy)
- 2x M2x10 mm self tapping
- 4x 6 mm x 3 mm magnets (N35 magnets work)

### Probe mount:

- 3x 6 mm x 3 mm magnets (N35 magnets work)
- 2x 22AWG cable (to connect the Klicky Probe to the control board)
- 2x M3x6 mm BHSC Screw

### Probe dock:

- 1x 6 mm x 3 mm magnets (N35 magnets work)
- 2x M3x16 mm

### Probe dock mounts:

- 2x M6x12 cap head bolt
- 2x M3 threaded insert M3x5 mmx4 mm

## Sourcing

To get the best experience, please consider purchasing from the trusted list of suppliers bellow.

[trusted suppliers list](./Sourcing.md)

## Parts location

The probe STL's are located [here](../../../Probes/KlickyProbes/STL).

The printer specific STL's are located [here](./VCore3_STL).

## What to print

- 2x KlickyProbe_v2.stl (keeping a spare is always a good idea)
- Probe_Mount_v1.stl
- Probe_Dock_v2.stl
- Probe_Dock_Mount_v1.stl

printed parts

#### Helpers to pressfit the probe magnet

- Probe_magnet_pressfit_helper.st
- Probe_magnet_holder.stl
- probe_pressfit_helper.stl

### Printing instructions

Recommended printing settings:

* initial layer height:0,24
* layer height: 0.2mm
* bottom/top/perimeters: 4
* infill: more than 23%
* infill type: Cubic
* Thin walls: On

It was tested and printed with ABS and PETG, might work on other materials, if you try, let me know how it worked out.

## Assembly

### Step 1 - Dock mount and Probe Dock assembly 

- [ ] 2x M3 threaded insert M3x5 mmx 4 mm
- [ ] 1x 6 mm x 3 mm magnets
- [ ] 2x M3x16 mm
- [ ] Super Glue

Install your heat set threaded inserts in the holes shown below.



Install the magnet in the Probe dock, make sure that the magnet is fully inserted, it's top should be below the plastic.

Screw the dock onto the Dock mount with the two M3x16mm screws.

Secure the magnet with a dab of super glue (not a lot, just a drop).



Mount the Probe Dock to the front left extrusion, You will adjust the Z offset in a minute.

Klicky Dockmount attached

### Step 2: Probe Assembly

For the probe assembly you need the following parts:

- [ ] 1x microswitch
- [ ] 2x M2x10 mm self tapping
- [ ] 5x 6 mm x 3 mm magnets
- [ ] 22AWG cable
- [ ] 1.5mm Drill (optional)
- [ ] Multimeter to check for Continuity 
- [ ] Super Glue



Maybe you need to clear the holes for the microswitch, a 1.5mm drill bit should work fine.

Install the microswitch so that the arrow on the probe body is pointing to the little switch.

The best way to install the back magnet is to attach a magnet to the probe dock and slide the probe on the dock to insert some distance and the insert he remaining with a tool, it should be slightly below the plastic.



Then take your self tapping screws and screw the microswitch in place, the pins on the switch will contact the magnets once installed, that way making this a Normally Connected probe.



You want to install the magnets in the way that the ones which are connected to the microswitch, have the same polarity.

Before placing the switch magnets, use some super glue on the holes (not a lot, just a drop), avoid the wires and the top of the magnets.

The 3rd magnet should have the inverse polarity, wait until the system is complete and assembled before gluing the magnets, they might need adjustment to ensure a good fit on the mount.

You can use the included pressfit helpers to help in securing the probe when you are inserting the magnets.



There is no need for soldering, the probe microswitch connectors are press-fit on the magnets, they should remain with the top above the probe plastic.



As the last step of the probe assembly check if you have continuity between two magnets that connect to the switch.

If you have a normally closed switch (as you should), then you should have a current flow, so continuity is established. When you press the switch you should lose continuity. When you have a normally open switch then the behavior is the other way around.

### Step 3: Probe mount Assembly

For the probe mount assembly you need the following parts

- [ ] 3x 6 mm x 3 mm magnets
- [ ] 22AWG cable to connect the Klicky Probe
- [ ] 2x M3 x 12mm BHSC 
- [ ] Multimeter to check for Continuity 
- [ ] Super Glue

The probe mount wires are also connected with pressure from the magnets, you can use the probe magnets as a template to insert the probe mount magnets, it is easier that way, so that the magnets are not inserted the wrong way.



again, before placing the wire magnets, use some super glue on the holes (not a lot, just a drop), avoid the wires and the top of the magnets.

The 3rd magnet should have the inverse polarity, exacly like on the probe.

Wait until the system is complete and assembled before gluing the 3rd magnets, they might need adjustment to ensure a good fit on the probe.

After everything is assembled let's check again for continuity, this time joining the ends of the cable and testing connectivity on the two wire magnets that have a cable.

### Step 4: Probe Mount installation and wiring

For the installation you need the following parts:

- [ ] 2x M3x12 mm BHSC Screws



Route the probe mount cables between the probe mount and the fan duct and then up the side of the EVA backplate. When installing the mount be careful not to push the hex nuts out of their grooves. It is a pain to take apart the EVA assembly to put them back in.

**Before going further, please turn off the printer, the boards are very picky with short circuits.**

Connect the probe to the controller board. You may also put an inline connector (I chose to do this) to enable easier switching in the future.

When testing the docking and attachment of the probe, make sure that the back magnet of the probe and the dock magnet do not touch, if they do, it will make attaching the probe much harder.

### Step 5: klipper configuration

As of right now, klipper and RRF have no inbuilt support for a removable probe, fortunately, it does support very robust macro programming, so you will need to add macros to be able to dock and attach the probe as necessary, as well as supporting the rest of the functions that require the usage of a probe.

The macros and instructions on how to configure are located on the [Macro directory](../../../Klipper_macros), you need to **check that before continuing on the build**, there are also some [RRF scripts](../../RRF_macros) that work.

This guide will assume users are using RATOS for their printer. It is probably easier to follow the generic Voron installation instructions if using a standard klipper installation.

Add all the klicky macros to the config directory (same level as your printer.cfg file.)

Update printer.cfg with the following changes:

Add the include line for the klicky probe

```python
#############################################################################################################
### HOMING
### Pick your probe and endstops
#############################################################################################################
# BL Touch
#[include config/z-probe/bltouch.cfg]
# Inductive/Capacitive probe
[include config/z-probe/probe.cfg]
[include klicky-probe.cfg]
```

Comment out the bltouch line if using and uncomment the probe line. Add line specifying that the probe is now connector to the z endstop pin (check your boards pinout to get the pin number). Comment out the whole safe z homing section

```python
# Z Probe configuration
#[bltouch]
#z_offset: 0.0 # Adjust this to fit your setup
[probe]
#z_offset: 0.0 # Adjust this to fit your setup
pin=PG10 # Added because using Z endstop pin as probe pin
#pin: ^probe_pin # For NPN NC probes such as the Super Pinda / Vinda / SupCR / Decoprobe probes.
#pin: ^!probe_pin # NPN NO (refer to the specs on your probe)
#pin: probe_pin # PNP NO (refer to the specs on your probe)
#pin: !probe_pin # PNP NC (refer to the specs on your probe)

# Safe Z Home (Physical endstops only)
#[safe_z_home]
#home_xy_position: 150,150 # 300mm printer
#home_xy_position: 200,200 # 400mm printer
#home_xy_position: 250,250 # 500mm printer
```
In the user overides section add the following section.

```python
[probe]
x_offset: -24.526
y_offset: -20.725
```

#### Assembled Klicky Probe

See assembled probe in action on youtube [here](https://youtu.be/aWnHNNrViP0)

### Step 6: klipper  Dock/Undock  configuration

#### Adjust Probe Pickup Position

One of the last things we need to do is to adjust the probe pickup position. I suggested manually moving the print head into position and use that to set your probe dock mount z height on the extrusion.

Turn your printer on and then make sure that the x and y axis are homed and the probe is manually attached to mount.

Now manually (with gcode commands) move the toolhead to the probe dock and move it so far to the back that the probe docks, note the Y-Position.

Next, again manually, move the toolhead parallel to the probe dock until the probe it is perfectly aligned with the mount, note the X.Position.

Open your `klicky-variables.cfg` and find the `#dock location` section and edit the following two line

```python
variable_docklocation_x:
variable_docklocation_y:
```

Test now with the ATTACH_PROBE and DOCK_PROBE if it docks and is removed correctly, some common points that can give problems are:

* the dock magnet is touching the back probe magnet, they cannot touch, push them further in
* the probe is hitting the dock arms, please move the toolhead more to the side where the probe does not hit, by 1mm at a time, until it works
* the probe is falling after being release, the dock is too far away, you can insert one or several 1mm spacer to move the dock and solve this

***WARNING when you are doing PROBE_ACCURACY, make sure that the probe is above the bed, the PROBE_ACCURACY macro does not move the toolhead in X or Y.***

Congratulations, your done :).

## Firsts tests

Before starting to test klicky, and from past mistakes, please remove your PEI sheet (the probe works on the magnetic sheet) and if possible, change your printer maximum speed, acceleration and Z current, on klipper with TMC steppers, you can do this:

```python
SET_TMC_CURRENT STEPPER=stepper_z CURRENT=0.2 
SET_VELOCITY_LIMIT ACCEL=1000
SET_VELOCITY_LIMIT VELOCITY=50
```

Enjoy your Klicky Probe!

## Dock and undock video

https://youtu.be/qqRuQJcBS7o

It is working very well, if you decide to use it, give me feedback, either here, or on discord, my discord user is Slzer#2881. Also a massive shoutout to JosAr#0517 who create the Klicky, all I did was modify it for the VCore3.

For help using or installing Klicky take a look at the guides posted on my blog [3DPandME](https://www.3dpandme.com/) or join the [discord](https://discord.gg/kKj9epxn7B) 

By standing on the shoulders of giants, lets see if we can see further.

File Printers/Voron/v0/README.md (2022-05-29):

# Klicky Probe for  Vorondesign v0 printers

Here you will find the necessary files and documentation to print and setup your own klicky probe on the v0 (and v0.1)

This directory has the STL files properly oriented for printing and community mods for the respective printer, there are [klipper](../../../Klipper_macros) macros and [RRF](../../../RRF_macros) macros on the repository.

You can find more information about the Voron printers at the [website](https://vorondesign.com/) or go check the [discord](https://discord.gg/voron), for the record, i own a v2.4, this is how i would describe them "A Voron is a fast high quality printer, i print with much better quality  the perimeters at the draft speed of my old bedslinger. It also has a  big community with lots of documentation and new ideas."

With an integrated mount, the bed can be fully used during printing, the bed only cannot be probed (at most) 6mm on the left side, this is due to the design of the probe, that extends below the nozzle.

There are currently two other probes available to use on the V0.1, Slideswipe and Sideswipe.

Above all, have fun and be excellent to one another, now to the instructions.

This mod is not yet on [VoronUsers repository](https://github.com/VoronDesign/VoronUsers/tree/master/printer_mods/JosAr/Klicky-Probe), should be soon. 

V2.4 Klicky Probe

## Mounting options

### Probe dock mount

The probe dock is mounted to the front right extrusion, where it minimizes the chance of being removed inadvertently during printing, like this:

Klicky Dockmount attached

There are several mounting options, depending on your setup:

It can be frustrating on the v0 to add extra m3 nuts on the 1515 extrusion after the assembly is complete, so there are several screwless probe dock options to avoid that scenario.

| Screwless variable | Fixed | Fixed extrabeef | Top screws | Side screws |
| :---: | :---: | :---: | :---: | :---: |
|  |  |  |  |  |
| recommended for most setups, does not require extra m3 nuts on the extrusion (v0.0/1) | fixed position, does not require extra m3 nuts on the extrusion (v0.1) | fixed, fits X carriages that are 2mm thicker, does not require extra m3 nuts on the extrusion(v0.1) | fixed, requires 2 extra m3 nuts on the top extrusion (v0.1) | fixed, requires 2 extra m3 nuts on the front extrusion (v0.1) |

There are also some more mounting options on [Usermods](./Usermods/), like a servo powered dock. ***Check it out***

### Probe toolhead mount

The v0 toolhead was not designed to use a probe, so there is no inbuilt location to add one, so i designed two options for the v0.1 variant and one for the original v0.

#### Front cowling mount (v0.1)

You can install a mount the attaches to the front of the toolhead cowling, it will need 2/3mm of X space on the front right of the bed to avoid picking the probe up by accident, it is very easy to install, it's ideal to test the concept of probing on the v0.1

| Front cowling mount | Front cowling mount |
| --- | --- |

You will require 2x M3 x 40mm (BHSC preferably) that are not on the V0(.1) BOM, there is an included wire path with zip tie support, to keep your printer looking good.

#### Integrated cowling (v0.1)

You can replace the cowling with a version that has a cutout to allow the klicky mount to attach, it has no impact on the cooling performance of the probe, it also includes a wire path to the back of the miniAB.

| Integrated klicky cowling | Klicky mount |
| --- | --- |

This method allow mounting of different probes on the V0.1, currently only klicky uses this mount, hopefully that can change in the future.

It also allows to pick up the probe at X121, effectively outside the bed, incurring in a no print space lost.

#### Fan duct mount (v0.0)

On the V0.0, you do not need to reprint the entire cowlink, you only need to replace the right fan duct with a version that has a mount for klicky, it has no impact on the cooling performance of the probe, it also includes a wire path to the back of the miniAB.

| V0 fan duct | Klicky |
| --- | --- |

This version has seen little tests because of the lack of a sufficient number of v0.0 to test on.

If you end up using this version, please tell me at what X do you dock and attach the probe.

It is also necessary to use the Screwless variable dock mount 

## Bill of Materials (BOM)

### Tools:

- 1.5mm Drill (optional)
- Multimeter to check for Continuity 
- Super Glue (optional)
- Soldering Iron

### Probe:

- 1x microswitch (the omron D2F-5 or D2F-5L (removing the lever is required), other also work with reduced accuracy or repeatability (mostly anecdotal evidence, needs a proper sudy)
- 2x M2x10 mm self tapping
- 10cm of 22AWG cable (to wire the magnets to the switch)
- 5x 6 mm x 3 mm magnets (N35 magnets work)

### Probe mount:

| Front cowling mount (v0.1) | Integrated cowling mount (v0.1) | Fan duct mount (v0.0) |
| --- | --- | --- |
| 4x 6 mm x 3 mm magnets (N35 magnets work) | 4x 6 mm x 3 mm magnets (N35 magnets work) | 4x 6 mm x 3 mm magnets (N35 magnets work) |
| 2x 20cm 22AWG cable (to connect the Klicky Probe to the umbilical termination point) | 2x 20cm 22AWG cable (to connect the Klicky Probe to the umbilical termination point) | 2x 20cm 22AWG cable (to connect the Klicky Probe to the umbilical termination point) |
| two wires to connect the controller to the extruder motor vicinity | two wires to connect the controller to the extruder motor vicinity | two wires to connect the controller to the extruder motor vicinity |
| 2x M3 x 40mm BHSC | 1x M3x6 mm BHSC Screw | 1x M3x6 mm BHSC Screw |
| | 1x M3 threaded insert M3x5 mmx4 mm | 2x M3 threaded insert M3x5 mmx4 mm |

### Probe dock:

- 1x 6 mm x 3 mm magnets (N35 magnets work)
- 2x M3x16 mm

### Probe dock mounts:

| Screwless variable (v0.0/1) | Fixed (v0.1) | Fixed extrabeef (v0.1) | Top screws (v0.1) | Side screws (v0.1) |
| :---: | :---: | :---: | :---: | :---: |
| 2x m3 nut | 2x M3 threaded insert M3x5 mmx4 mm | 2x M3 threaded insert M3x5 mmx4 mm | 2x M3 threaded insert M3x5 mmx4 mm | 2x M3 threaded insert M3x5 mmx4 mm |
| | | | 2x m3x8 mm | 2x m3x8 mm |

## Sourcing

To get the best experience, please consider purchasing from the trusted list of suppliers bellow.

[trusted suppliers list](./Sourcing.md)

## Parts location

The probe STL's are located [here](../../../Probes/KlickyProbes/STL).

The printer specific STL's are located [here](./v0_STL).

The CAD with all the parts are [here](../../../CAD).

## What to print

### Probe 

* 2x KlickyProbe_Long_v2.stl (keeping a spare is always a good idea)

The KlickyProbe_v2.stl is also compatible, but has a different Y offset and cannot probe all the bed.

#### Helpers to pressfit the probe magnet

* Probe_magnet_pressfit_helper.stl

* Probe_magnet_holder.stl

* Longer_probe_pressfit_helper.stl

### Probe mount

| Front cowling mount (v0.1) | Integrated cowling mount (v0.1) | Fan duct mount (v0.0) |
| --- | --- | --- |
| Front_cowling_mount.stl | MiniAB_Dragon_Cowling_wKlicky.stl | V0_Fan_duct_wKlicky.stl |
| v0.1_integrated_mount.stl  | v0.1_integrated_mount.stl | v0_integrated_mount.stl |

There are also other integrated cowlings, check the [STL] folder, namely, the Serpa_Mini_Dragon_Cowling_wKlicky.stl from [Kyrios](https://github.com/KurioHonoo/Mini-AfterSherpa) and the LGX Lite cowling from [Bondtech](https://www.bondtech.se/2021/12/27/voron-v0-1-toolhead-setup-for-lgx-lite/).

### Probe dock

* Probe_Dock_v2.stl

### Probe dock mounts

| Screwless variable (v0.0/1) | Fixed (v0.1) | Fixed extrabeef (v0.1)  | Top screws (v0.1) | Side screws (v0.1) |
| --- | --- | --- | --- | --- |
| DockMount_variable.stl | DockMount_fixed.stl | DockMount_extrabeef.stl | DockMount_TopScrews.stl | DockMount_SideScrews.stl |

### Printing instructions

Recommended printing settings:

* initial layer height:0,24
* layer height: 0.2mm
* bottom/top/perimeters: 4
* infill: more than 23%
* infill type: Cubic
* Thin walls: On

It was tested and printed with ABS, might work on other materials, if you try, let me know how it worked out.

### Typical V0.1 components

Klicky v0.1 components

(the images with the green background were provided by user SunB#1489 and are being used with permission).

## Assembly

### Step 1 - Dock mount and Probe Dock assembly 

In this examples, the Fixed dock will be used.

- [ ] 2x M3 threaded insert M3x5 mmx 4 mm
- [ ] 1x 6 mm x 3 mm magnets
- [ ] 2x M3x16 mm
- [ ] Super Glue

Here we will use the Fixed dock as an example, the other docks are very similar.

Install your heat set threaded inserts like you did within your Voron build. 



Install the magnet in the Probe dock, make sure that the magnet is fully inserted, it's top should be below the plastic.

Screw the dock onto the Dock mount with the two M3x16mm screws.

Secure the magnet with a dab of super glue (not a lot, just a drop).



Mount the Probe Dock to the front right extrusion, snap first on the front extrusion, then on the top one (do this after assembling the probe).

Klicky Dockmount attached

### Step 2: Probe Assembly

For the probe assembly you need the following parts:

- [ ] 1x microswitch
- [ ] 2x M2x10 mm self tapping
- [ ] 5x 6 mm x 3 mm magnets
- [ ] 10cm of 22AWG cable
- [ ] 1.5mm Drill (optional)
- [ ] Multimeter to check for Continuity 
- [ ] Super Glue



Maybe you need to clear the holes for the microswitch, a 1.5mm drill bit should work fine.

Install the microswitch so that the arrow on the probe body is pointing to the little switch.

The best way to install the back magnet is to attach a magnet to the probe dock and slide the probe on the dock to insert some distance and the insert he remaining with a tool, it should be slightly below the plastic.



Then take your self tapping screws and screw the microswitch in place, you should also now solder the wires to the outside pins of the switch, that way making this a Normally Connected probe.



You should place the wires cover outside the ducts to the magnets and install them in the space below the magnets, more like the right wire is on the image below.



You want to install the magnets in the way that the ones which are connected to the microswitch, have the same polarity.

Before placing the switch magnets, use some super glue on the holes (not a lot, just a drop), avoid the wires and the top of the magnets.

The 3rd magnets (there are two) should have the inverse polarity, wait until the system is complete and assembled before gluing the magnets, they might need adjustment to ensure a good fit on the mount.

You can use the included pressfit helpers to help in securing the probe when you are inserting the magnets.



There is no need for soldering, the probe microswitch connectors are press-fit on the magnets, they should remain with the top above the probe plastic.



As the last step of the probe assembly check if you have continuity between two magnets that connect to the switch.

If you have a normally closed switch (as you should), then you should have a current flow, so continuity is established. When you press the switch you should lose continuity. When you have a normally open switch then the behavior is the other way around.

### Step 3: Probe mount Assembly

In this example, the Front cowling mount will be used.

For the Front cowling mount assembly you need the following parts

- [ ] 4x 6 mm x 3 mm magnets
- [ ] 2 x 20cm 22AWG cable to connect the Klicky Probe to the Mircofit Terminal
- [ ] two wires to connect the controller to the extruder motor vicinity
- [ ] some microfit or jst hardware
- [ ] 2x M3 x 40mm BHSC 
- [ ] Multimeter to check for Continuity 
- [ ] Super Glue

The probe mount wires are also connected with pressure from the magnets, you can use the probe magnets as a template to insert the probe mount magnets, it is easier that way, so that the magnets are not inserted the wrong way.

again, before placing the wire magnets, use some super glue on the holes (not a lot, just a drop), avoid the wires and the top of the magnets.

The 3rd magnets (there are two) should have the inverse polarity, exacly like on the probe.

Wait until the system is complete and assembled before gluing the 3rd magnets, they might need adjustment to ensure a good fit on the probe.

|  |  |  |
| :---: | :---: | --- |

(The mount has since been improved a bit to avoid cracking)

After everything is assembled let's check again for continuity, this time joining the ends of the cable and testing connectivity on the two wire magnets that have a cable.

### Step 4: Probe Mount installation and wiring

For the installation you need the following parts:

- [ ] 2x M3x40 mm BHSC Screws



Route the probe mount cables to near the end of the V0 umbilical, install a male terminal in there.

**Before going further, please turn off the printer, the SKR boards are very picky with short circuits.**

Connect a female terminal to the wires that will run in the umbilical from the toolhead to the controller.



Connect the wires from the Klicky Probe to the Zprobe port, on GND and PC14 bin (I reused the LDO kit connector)

|  | v0_eletronic |
| --- | --- |

When testing the docking and attachment of the probe, make sure that the back magnet of the probe and the dock magnet do not touch, if they do, it will make attaching the probe much harder.

### Step 5: klipper configuration

Unfortunately, I do not know how to document RRF probe configuration, so here is only Klipper configurations.

As of right now, klipper and RRF have no inbuilt support for a removable probe, fortunately, it does support very robust macro programming, so you will need to add macros to be able to dock and attach the probe as necessary, as well as supporting the rest of the functions that require the usage of a probe.

The macros and instructions on how to configure are located on the [Macro directory](../../../Klipper_macros), you need to **check that before continuing on the build**, there are also some [RRF scripts](../../RRF_macros) that work for the Voron V2.4.

For the Voron v0, these are the recommended configuration on the klicky-variables.cfg:

```python
variable_verbose:               True  # Enable verbose output
variable_travel_speed:          100   # how fast all other travel moves will be performed when running these macros
variable_dock_speed:            50    # how fast should the toolhead move when docking the probe for the final movement
variable_release_speed:         55    # how fast should the toolhead move to release the hold of the magnets after docking
variable_z_drop_speed:          20    # how fast the z will lower when moving to the z location to clear the probe
    
variable_safe_z:         	    25    # Minimum Z for attach/dock and homing functions
# if true it will move the bed away from the nozzle when Z is not homed
variable_enable_z_hop:        True    # True v0
    
#Dock move
Variable_dockmove_x:             0    # Final toolhead movement to release
Variable_dockmove_y:            40    # the probe on the dock
Variable_dockmove_z:             0    # (can be negative)

#Attach move
Variable_attachmove_x:          30    # Final toolhead movement to Dock
Variable_attachmove_y:           0    # the probe on the dock
Variable_attachmove_z:           0    # (can be negative)
    
variable_max_bed_x:             120   # maximum Bed size avoids doing a probe_accuracy outside the bed
variable_max_bed_y:             120   # maximum Bed size avoids doing a probe_accuracy outside the bed

```

The sections below should be added to klicky-specific.cfg, that way, it will be loaded on klipper via a klicky-probe.cfg include.

If you would like to use a bed mesh, this is the recommended settings:

```python
[bed_mesh]
mesh_min: 15,15
mesh_max: 105,105
speed: 100
horizontal_move_z: 20 

probe_count: 3,3					#if you would like more detail, use 5,5 here
relative_reference_index: 4			 #if you use 5,5 above, place 12 here
move_check_distance: 3

algorithm: lagrange
fade_start: 1
fade_end: 10
fade_target: 0
split_delta_z: 0.0125
mesh_pps: 2,2
```

Regarding the Screws Tilt Adjust (Klipper probes the three screws positions and recommends the number of turns to level the bed), you can use this configuration as a reference, the probe should be over the screws when you do send the nozzle to the respective coordinate:

```python
[screws_tilt_adjust]
screw1: 100,115          #For Long probe
screw1_name: back right
screw2: 0,115            #For Long probe
screw2_name: back left
screw3: 60,5             #For Long probe
screw3_name: front screw
horizontal_move_z: 20
speed: 100
screw_thread: CW-M3
```

You should test this and adjust accordingly. 

This is probe configuration is with the default Voron v0.1 SKR mini E3 v2 configuration, with the probe connected to the PC14 pin, please update it to your specific configuration:

```python
[probe]
#with Long Klicky Probe
pin: ^PC14
x_offset: 8 #(9.5 with front cowling)
y_offset: 0
z_offset: 14.5
speed: 7
lift_speed: 7

samples: 3
samples_result: median
sample_retract_dist: 2

samples_tolerance: 0.01
samples_tolerance_retries: 10
```

I recommend a probing speed between 5mm/s and 10mm/s, you may experiment to see what is the better speed for your machine.
Please confirm that if you are not using a endstop pin, that the pull-up is enable by using the ^ sign, normally the endstop pins have a hardware solution that does not require this configuration.
Depending on your switch you may need to add a `!` to invert that pin (normally open vs. normally closed).

#### Z endstop and Probe configuration (virtual Z endstop)

If you want to use the Klicky Probe as your Z endstop, please read this [excellent documentation](https://github.com/T4KUUY4/Voron-Stuff/tree/main/KlickyProbeZoffset) by Takuya and Clee, as it was written for a Voron v2.4 you need to use the probe offsets that are defined in here.

#### Assembled Klicky Probe

Assembled Klicky Probe

### Step 6: klipper  Dock/Undock  configuration
#### X max position adjustment

Even in the stock X endstop with a lever, you normally can add a extra mm of X travel due to the lever extra trigger distance:

```python
[stepper_x]
position_endstop: 120
position_max: 121
```

#### Adjust Probe Pickup Position

One of the last things we need to do is to adjust the probe pickup position.

Make sure that the x and y axis are homed and the probe is manually attached to mount.

Now manually (with gcode commands) move the toolhead to the probe dock and move it so far to the back that the probe docks, note the Y-Position.

Next, again manually, move the toolhead parallel to the probe dock until the probe it is perfectly aligned with the mount, note the X.Position.

Open your `klicky-variables.cfg` and find the `#dock location` section and edit the following two line

```python
variable_docklocation_x:
variable_docklocation_y:
```

Test now with the ATTACH_PROBE and DOCK_PROBE if it docks and is removed correctly, some common points that can give problems are:

* the dock magnet is touching the back probe magnet, they cannot touch, push them further in
* the probe is hitting the dock arms, please move the toolhead more to the side where the probe does not hit, by 1mm at a time, until it works
* the probe is falling after being release, the dock is too far away, you can insert one or several 1mm spacer to move the dock and solve this

***WARNING when you are doing PROBE_ACCURACY, make sure that the probe is above the bed, the PROBE_ACCURACY macro does not move the toolhead in X or Y.***

Congratulations, your done :).

## Firsts tests

Before starting to test klicky, and from past mistakes, please remove your PEI sheet (the probe works on the magnetic sheet) and if possible, change your printer maximum speed, acceleration and Z current, on klipper with TMC steppers, you can do this:

```python
SET_TMC_CURRENT STEPPER=stepper_z CURRENT=0.2 
SET_VELOCITY_LIMIT ACCEL=1000
SET_VELOCITY_LIMIT VELOCITY=50
```

Enjoy your Klicky Probe!

## Dock and undock video

https://youtu.be/qqRuQJcBS7o

It is working very well, if you decide to use it, give me feedback, either here, or on discord, my discord user is JosAr#0517.

By standing on the shoulders of giants, lets see if we can see further.

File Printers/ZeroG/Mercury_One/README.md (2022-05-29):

# Klicky Probe for Zero G Mercury One printers
Here you will find the necessary files and documentation to print and setup your own klicky probe on the [Zero G Mercury One](https://github.com/ZeroGDesign/Mercury).

This directory has the STL files properly oriented for printing and community mods for the respective printer, there are [klipper](../../../Klipper_macros) macros and [RRF](../../../RRF_macros) macros in the repository.

The Zero G Mercury is a Voron-inspired 3D printer conversion that turns Creality Ender 5, 5 Pro and 5 Plus machines into high-performance, klipper-based CoreXY printers.  You can find more information about the project at the [Zero G website](https://zerog.one/index.html) or the [Zero G Mercury One github](https://github.com/ZeroGDesign/Mercury), or go check their [discord](https://discord.com/invite/gzJP2s8).

## Mounting options

There are two supported gantry configurations for the Mercury One:
- *EVA*: This is the standard gantry, compatible with toolheads from the [EVA project](https://main.eva-3d.page/) project.
- *Voron Afterburner / Stealthburner*: This gantry supports the same toolheads as the Voron 2.4.

### Sourcing

To get the best experience, please consider purchasing from the trusted list of suppliers bellow.

[trusted suppliers list](./Sourcing.md)

### EVA Probe dock mount

Coming soon...

### Voron Afterburner / Stealthburner Probe dock mount

The probe dock is mounted to the rear extrusion just to the right of the leftmost Z-axis bracket:

Klicky Dock Closeup
Klicky Dock Location

> Note: The dock can be mounted slightly outside of the Y-axis build volume to help avoid unintentional probe mounting while printing.  If you want to do this, you will need to adjust your Y endstop (physically) and your `[stepper_y]` `position_max` in `printer.cfg` to make sure the toolhead can reach the probe dock.

### Probe toolhead mount

The probe is mounted to the Afterburner / Stealthburner gantry bracket inside the cavity for the inductive probe. It can be used as a Z-probe for bed mesh leveling and as a Z endstop for perfect first layers on any bed.

### Printed parts
There is no need for supports, all the files are ready to print, they are in the recommended orientation.

The Klicky Probe consists of four different components:

- Toolhead components, found in the [Voron 2.4 STL directory](../../Voron/v1.8_v2.4_Legacy_Trident/v1.8_v2.4_Legacy_Trident_STL/):
    - [`KlickyProbe_AB_mount_v2.stl`](../../Voron/v1.8_v2.4_Legacy_Trident/v1.8_v2.4_Legacy_Trident_STL/KlickyProbe_AB_mount_v2.stl)
    - [`Mount_magnet_holder.stl`](../../Voron/v1.8_v2.4_Legacy_Trident/v1.8_v2.4_Legacy_Trident_STL/Mount_magnet_holder.stl)
    - [`Mount_magnet_pressfit_helper.stl`](../../Voron/v1.8_v2.4_Legacy_Trident/v1.8_v2.4_Legacy_Trident_STL/Mount_magnet_pressfit_helper.stl)
    - [`Mount_pressfit_holder.stl`](../../Voron/v1.8_v2.4_Legacy_Trident/v1.8_v2.4_Legacy_Trident_STL/Mount_pressfit_holder.stl)
- The probe itself, found in the [KlickyProbe directory](../../../Probes/KlickyProbe/STL), [KlickyProbe_v2](../../../../Probes/KlickyProbe/STL/KlickyProbe_v2.stl) 
- Probe dock, found in the [base STL directory](../../../Probes/KlickyProbe/STL/), [Probe_Dock_v2](../../../../Probes/KlickyProbe/STL/Probe_Dock_v2.stl) 
- Frame dock mount from the [Voron_Toolhead_STL](./Voron_Toolhead_STL/) folder ([CAD models](./Voron_Toolhead_CAD/) are also available)

The recommended printing configuration is:

* initial layer height: 0.24
* layer height: 0.2mm
* bottom/top/perimeters: 4
* infill: more than 23%
* infill type: Cubic
* Thin walls: On

## Assembly

### Steps 1 through 4
Follow assembly steps 1 through 4 in the [Voron 2.4 instructions](/../../Voron/v1.8_v2.4_Legacy_Trident#assembly).

Make sure to print and use the dock mount in [Voron_Toolhead_STL](./Voron_Toolhead_STL) and install the heat set inserts:



### Step 5: klipper configuration

Unfortunately, I do not know how to document RRF probe configuration, so here is only Klipper configurations.

As of right now, klipper and RRF have no inbuilt support for a removable probe, fortunately, it does support very robust macro programming, so you will need to add macros to be able to dock and attach the probe as necessary, as well as supporting the rest of the functions that require the usage of a probe.

The macros and instructions on how to configure are located on the [Macro directory](../../../Klipper_macros), you need to **check that before continuing on the build**, there are also some [RRF scripts](../../RRF_macros).

For the printers that are covered here, this is the recommended configuration in `klicky-variables.cfg`:

```python
variable_verbose:               True  # Enable verbose output
variable_travel_speed:          200   # how fast all other travel moves will be performed when running these macros
variable_dock_speed:            50    # how fast should the toolhead move when docking the probe for the final movement
variable_release_speed:         75    # how fast should the toolhead move to release the hold of the magnets after docking
variable_z_drop_speed:          20    # how fast the z will lower when moving to the z location to clear the probe

variable_safe_z:         	    25    # Minimum Z for attach/dock and homing functions
# If true it will move the bed away from the nozzle when Z is not homed

variable_enable_z_hop:          True  # set this to false for beds that fall significantly under gravity (almost to Z max)

# Dock move (the final movement required to reach the dock and avoid the arms with the probe attached)
Variable_dockmove_x:            40    # Final toolhead movement to release
Variable_dockmove_y:            0     # the probe on the dock
Variable_dockmove_z:            0     # (can be negative)

# Attach move (the final movement required release the probe on the dock)
Variable_attachmove_x:          0     # Final toolhead movement to Dock
Variable_attachmove_y:          30    # the probe on the dock
Variable_attachmove_z:          0     # (can be negative)

variable_docklocation_z:      -128    # Z dock position (-128 for a gantry/frame mount)
```

This is an example `printer.cfg` configuration for a BigTreeTech Octopus Pro, with the Klicky probe connected to the `PC5` probe pin, please update it to your specific configuration.  It is recommended to set the probe voltage on the Octopus to `5v` instead of the default `24v`.  Alternatively, you can use a normal endstop pin for the Klicky probe.

```python
[probe]
pin: PC5 # Set the Octopus jumper to 5v instead of the default 24v!
x_offset: -1.5
y_offset: 19.75
z_offset: 7.450
speed: 2.5
samples: 3
samples_result: median
sample_retract_dist: 2.0
samples_tolerance: 0.01
samples_tolerance_retries: 5

[bed_mesh]
speed: 120
horizontal_move_z: 10
mesh_min: 20, 24
mesh_max: 210, 190 # Ender 5 / 5 Pro
#mesh_max: 340, 310 # Ender 5 Plus
probe_count: 5,3
```

I recommend a probing speed between 5mm/s and 10mm/s, you may experiment to see what is the better speed for your machine.
Please confirm that if you are using the probe input, that the pull-up is enable by using the ^ sign, normally the endstop pins have a hardware solution that does not require this configuration.
Depending on your switch you may need to add a `!` to invert that pin (normally open vs. normally closed).
Normally the endstop pins use a hardware solution, so it is not necessary.

There is now an arrow on the probe telling you where should the switch pole be to have the correct offset.

#### Z endstop and Probe configuration

If you want to use the Klicky Probe as your Z endstop (recommended), you need to change the `endstop_pin:` under the `[stepper_z]` section to `probe:z_virtual_endstop`.

Just comment out the old one and add a new line `endstop_pin: probe:z_virtual_endstop` and comment out `position_endstop`:

To use Klicky as a Z-endstop (recommended), you must update `printer.cfg`:
```python
[stepper_z]
endstop_pin: probe:z_virtual_endstop # Klicky probe Z endstop
#position_endstop: -0.10
```

You will need to update the `klicky-variables.cfg` Z probing variables, set the two variables below to `0`, it will probe the middle of the bed.

```python
variable_z_endstop_x:     0
variable_z_endstop_y:     0
```

#### Assembled Klicky Probe

Assembled Klicky Probe

### Step 6: klipper  Dock/Undock configuration

#### Adjust Probe Pickup Position

One of the last things we need to do is to adjust the probe pickup position.

Make sure that the x and y axis are homed and the probe is manually attached to mount, it is easier to do with the hotend and fan duct removed.

Now manually (with gcode commands) move the toolhead to the front of the probe dock, adjust X so that moving along Y does not hit the dock arms, ***note the X-Position***.

Example for a Ymax of `305`:

```gcode
G0 X20 Y270
G0 X20 Y280 (you see that the right side will hit the dock arm)
G0 X20 Y270
G0 X19 Y270
G0 X19 Y280 (still hitting the dock on the right side)
G0 X19 Y270
G0 X18 Y270
G0 X17 Y280 (now does not hit)
```
Your `variable_docklocation_x` is determined to be `17`

Now manually (with gcode commands) move the toolhead to the  X:`variable_docklocation_x`, Y:`max-40` position.
In the example above, it would be `G0 X17 Y265`.

The probe and dock magnet can be 1/2 mm away from each other, that is ok, they will attach when the probe is released from the mount.

Now move the toolhead 40mm to the side and check if the probe is docked securely.
If it does, perfect, variable_docklocation_y is your `Ymax`, if not, you need to either increase the `Ymax` or add a dock extender and repeat the process.

Open your `klicky-variables.cfg` and find the `#dock location` section and edit the following two lines

```python
variable_docklocation_x:
variable_docklocation_y:
```

Test now with the `ATTACH_PROBE` and `DOCK_PROBE` macros to see if it docks and is removed correctly, some common points that can give problems are:

* the dock magnet is touching the back probe magnet, they cannot touch, push them further in
* the probe is hitting the dock arms, please move the toolhead more to the side where the probe does not hit, by 1mm at a time, until it works
* the probe is falling after being release, the dock is too far away, you can insert one or several 1mm spacer to move the dock and solve this

#### Probe_accuracy and Probe_calibrate

> ***WARNING***: when you are doing `PROBE_ACCURACY`, make sure that the probe is above the bed, the `PROBE_ACCURACY` macro does not move the toolhead in X or Y.

## Firsts tests

Before testing klicky, and from past mistakes, please remove your PEI sheet (the probe works on the magnetic sheet) and

If possible, change your printer maximum speed, acceleration and Z current, on klipper with TMC steppers, this is how you do it:

```python
SET_TMC_CURRENT STEPPER=stepper_z CURRENT=0.6
SET_TMC_CURRENT STEPPER=stepper_z1 CURRENT=0.6
SET_TMC_CURRENT STEPPER=stepper_z2 CURRENT=0.6
SET_TMC_CURRENT STEPPER=stepper_z3 CURRENT=0.6
SET_VELOCITY_LIMIT ACCEL=1000
SET_VELOCITY_LIMIT VELOCITY=100
```

Enjoy your Klicky Probe!

## Dock, undock and Z-endstop probing video
This video shows the docking, undocking and z-endstop probing process in a Zero G Mercury One

Klicky Probe in action (https://www.youtube.com/watch?v=HXm9AFOVeQQ)

It is working very well, if you decide to use it, give me feedback, either here, or on discord, my discord user is srkthain#6222.

By standing on the shoulders of giants, lets see if we can see further.

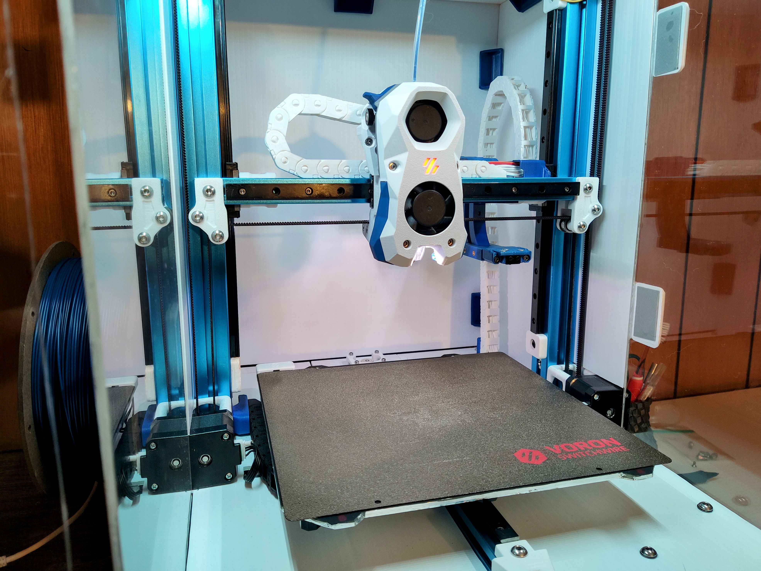
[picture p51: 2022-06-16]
Printers/Voron/Switchwire/Photos/IMG_20220606_1957072.jpg

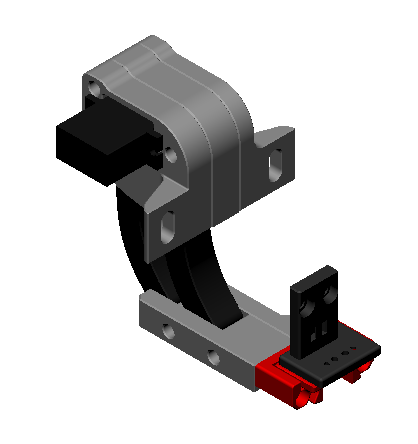
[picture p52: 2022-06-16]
Printers/Voron/Switchwire/Photos/sw_frontview.png

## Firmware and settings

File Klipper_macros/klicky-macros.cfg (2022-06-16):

# This macro was provided by discord user Garrettwp to whom i give my thanks for sharing it with me.
# I have tweaked it a lot.
# They are based on the great Annex magprobe dockable probe macros "#Originally developed by Mental,
# modified for better use on K-series printers by RyanG and Trails", kudos to them.
# That macro as since evolved into a klipper plugin that currently is pending inclusion in klipper, 
# more information here, https://github.com/Annex-Engineering/Quickdraw_Probe/tree/main/Klipper_Macros
# User richardjm revised the macro variables and added some functions
# User sporkus added led status notifications
# Thanks to all who helped,
# by standing on the shoulders of giants, lets see if we can see further
#
# the current home for this version is https://github.com/jlas1/Klicky-Probe 

[respond]

[gcode_macro _Probe_Variables]
variable_probe_attached:            False
variable_probe_state:               False
variable_probe_lock:                False
variable_z_endstop_x:               0
variable_z_endstop_y:               0
gcode:


#checks if the variable definitions are up to date
[gcode_macro _klicky_check_variables_version]
gcode:
    {% set version = printer["gcode_macro _User_Variables"].version|default(0) %}

    {% if version != 1 %}
        { action_raise_error("Please update your klicky variables, there are some functionality changes") }
    {% endif %}

[gcode_macro _KlickyDebug]
gcode:
    {% set message  = params.MSG %}
    {% set debug = printer["gcode_macro _User_Variables"].debug|default(False) %}
    
    {% if debug %}
        { action_respond_info(message) }
    {% endif %}    


[gcode_macro _exit_point]
gcode:
    {% set function  = 'pre_' ~ params.FUNCTION %}
    {% set move  = params.MOVE|default(0) %}
    {% set speed = printer["gcode_macro _User_Variables"].travel_speed %}

    # mandatory to save the new safe position
    M400
    SET_VELOCITY_LIMIT ACCEL={printer.configfile.settings.printer.max_accel}
    SET_VELOCITY_LIMIT ACCEL_TO_DECEL={printer.configfile.settings.printer.max_accel_to_decel}
    RESTORE_GCODE_STATE NAME={function} MOVE={move} MOVE_SPEED={speed}


[gcode_macro _entry_point]
gcode:
    {% set function  = 'pre_' ~ params.FUNCTION %}
    {% set move_accel = printer["gcode_macro _User_Variables"].move_accel|default(1000) %}
    # mandatory to save the new safe position
    M400
    SAVE_GCODE_STATE NAME={function}
    # removes the Z offset for better bed based docking
    SET_GCODE_OFFSET Z=0
    # all the macros initially assume absolute positioning
    G90
    # set a safe(sane) Acceleration
    SET_VELOCITY_LIMIT ACCEL={move_accel}

[gcode_macro _Homing_Variables]
gcode:
    {% set reset  = params.RESET|default(0) %}
    {% if reset %}
        SET_GCODE_VARIABLE MACRO=_Probe_Variables VARIABLE=probe_lock VALUE={ False }
    {% endif %}

##########################
# Attach probe and lock it
[gcode_macro Attach_Probe_Lock]
description: Attaches Klicky Probe, can only be docked after unlocking
gcode:
    Attach_Probe
    _Probe_Lock

########################
# Dock probe and lock it
[gcode_macro Dock_Probe_Unlock]
description: Docks Klicky Probe even if it was locked
gcode:
    _Probe_Unlock
    Dock_Probe

##############
# Unlock Probe
[gcode_macro _Probe_Unlock]
description: Unlocks Klicky Probe state
gcode:
    _KlickyDebug msg="_Probe_Lock setting probe_lock variable to False"
    SET_GCODE_VARIABLE MACRO=_Probe_Variables VARIABLE=probe_lock VALUE={ False }

############
# Lock Probe
[gcode_macro _Probe_Lock]
description: Locks Klicky Probe state
gcode:
    _KlickyDebug msg="_Probe_Lock setting probe_lock variable to True"
    SET_GCODE_VARIABLE MACRO=_Probe_Variables VARIABLE=probe_lock VALUE={ True }

###################
# Klicky Dock Servo Deploy

[gcode_macro _DeployKlickyDock]
description: Deploys Klicky servo-controlled dock
gcode:
    {% set enable_dock_servo = printer["gcode_macro _User_Variables"].enable_dock_servo|default(False) %}
    {% set servo_delay = printer["gcode_macro _User_Variables"].servo_delay|default(1000) %}
    {% set servo_name = printer["gcode_macro _User_Variables"].servo_name %}
    {% set servo_deploy = printer["gcode_macro _User_Variables"].servo_deploy|default(360) %}

    #wait for all the moves to complete
    M400
    {% if enable_dock_servo != False %}
        _KlickyDebug msg="_DeployKlickyDock Klicky servo configuration enabled"
        {% if servo_deploy == 360 %}
            { action_raise_error("Klicky: servo active on klicky-variables, but no servo deploy angle specified") }
        {% endif %}
        _KlickyDebug msg="_DeployKlickyDock SET_SERVO SERVO={servo_name|string} ANGLE={servo_deploy|int}"
        SET_SERVO SERVO={servo_name|string} ANGLE={servo_deploy|int}
        M400
        G4 P{servo_delay|int}
        _KlickyDebug msg="_DeployKlickyDock SET_SERVO SERVO={servo_name|string} WIDTH=0"
        SET_SERVO SERVO={servo_name|string} WIDTH=0
    {% elif printer["gcode_macro _DeployDock"] is defined %}
        _KlickyDebug msg="_DeployKlickyDock calling _DeployDock"	
        _DeployDock
    {% endif %}

####################
# Dock Servo Retract

[gcode_macro _RetractKlickyDock]
description: Retracts Klicky servo-controlled dock
gcode:
    {% set enable_dock_servo = printer["gcode_macro _User_Variables"].enable_dock_servo|default(False) %}
    {% set servo_delay = printer["gcode_macro _User_Variables"].servo_delay|default(1000) %}
    {% set servo_name = printer["gcode_macro _User_Variables"].servo_name %}
    {% set servo_retract = printer["gcode_macro _User_Variables"].servo_retract|default(360) %}
    
    #wait for all the moves to complete
    M400
    {% if enable_dock_servo != False %}
        _KlickyDebug msg="_RetractKlickyDock Klicky servo configuration enabled"
        {% if servo_retract == 360 %}
            { action_raise_error("Klicky: servo active on klicky-variables, but no servo retract angle specified") }
        {% endif %}
        _KlickyDebug msg="_RetractKlickyDock SET_SERVO SERVO={servo_name|string} ANGLE={servo_retract|int}"
        SET_SERVO SERVO={servo_name|string} ANGLE={servo_retract|int}
        M400
        G4 P{servo_delay|int}
        _KlickyDebug msg="_RetractKlickyDock SET_SERVO SERVO={servo_name|string} WIDTH=0"
        SET_SERVO SERVO={servo_name|string} WIDTH=0
    {% elif printer["gcode_macro _RetractDock"] is defined %}
        _KlickyDebug msg="_RetractKlickyDock calling _RetractDock"	
        _RetractDock
    {% endif %}
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

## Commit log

2022-05-29 pulling level command out of printer config
2022-05-30 adding reference to klicky-macros/probe_accuracy issue
2022-06-08 new version with screw in pin
    [UKNF screwpin.step, UKNG MFP.step, body (2.7mm magnet).stl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]
2022-06-08 fixed missing wire hole
    [UKNF screwpin.step, body 2.7mm.stl, body.stl]
2022-06-08 adding more meat back to body for auto-z
    [UKNF screwpin.step, body 2.7mm.stl, body.stl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]
2022-06-08 remove outdated print orientation
2022-06-08 fix pin stl orientation
    [pin.stl]
2022-06-09 2.7mm body in non-freedom units
    [body 2.7mm.stl]
2022-06-10 Improved pin action
    [body 2.7mm.stl, body.stl, cap.stl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]
